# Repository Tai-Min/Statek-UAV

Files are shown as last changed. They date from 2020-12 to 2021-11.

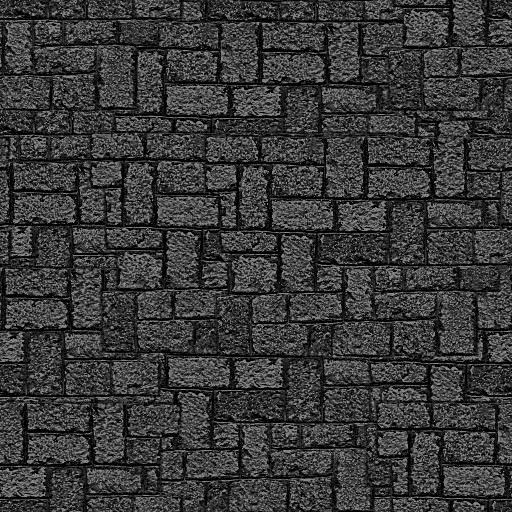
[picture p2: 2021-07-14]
catkin_ws/src/statek_sim/models/park_map/meshes/stone_dark.jpg

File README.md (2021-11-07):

# Statek-UAV
ROS based UAV, Master's degree final project.

This repository consists of CAD files for the chassis, CAD files for electronic boards, catkin workspace for all ROS nodes created for the project and some additional scripts used during development.

The core part of this project is the real, 3D printed vehicle along with all the hardware attached to it (Jetson Nano B01 for main controller and STM32f103RBT6 for real time core). 

The software part of this project can be split into real time (closed loop wheel control), short term navigation (movement between two GPS waypoints) and long term navigation (navigation through series of GPS waypoints).
During the project's development, my main focus was on short term navigation, which is also the biggest and most complicated part of the project. Short term navigation stack
consists of static local map generator, dynamic local map generator (human leg detector mostly based on U-Net fully convolutional neural network), Voronoi graph generator, A* path planner and non linear model predictive controller for navigation.

For more info see [this arcitle](https://www.hackster.io/Tai-Min/statek-uav-ff225e).

**Just to warn you:** If you want to use this project somehow, use it as reference only. It is NOT meant to be assembled as it contains some design flaws both in hardware
and software that I don't intent to fix in this iteration of the project as code in this repository will stay in unchanged since the moment I handed over my thesis.
Most of the files in the "instructions" folder consists of the steps I've did to setup my hardware and Ipopt solver. Those might not work for you/could be dangerous (I might've abused sudo a bit) so use them at your own risk. The code quality depends on the time I had untill the deadline to hand over my thesis. In my opinion it should be fine for the most part, well documented and easy to follow but judge for yourself.

**Disclaimer:** I've tried to credit all authors of 3D files used in the project. All of the models had permissive license allowing me to use them.
If you see your work here without being credited or you just don't want to have your files used here - open an issue on this project and I'll fix any problems.

The files in this folder have the following structure:
* CAD
  * detailed - Inventor files for the 3D printing and assembling.
  * low_poly - Inventor files for simple low poly model for Gazebo and Rviz.
* catkin_ws/src
  * statek - Metapackage for the project
  * statek_calibrate - Calibration algorithms for cameras, GPS Kalman filter, IMU, Motor's PI controller autotuning. 
  * statek_config - Config files for the robot, including transformations, urdf and parameters for ROS nodes.
  * statek_hw - code to launch hardware based nodes (lidar, rosserial, cameras etc.) along with source code for real time controller.
  * statek_map - Mapping algorithms (dynamic local mapper, voronoi generator and GPS to hyperplane casting).
  * statek_ml - Leg detector based mostly on U-net fully convolutional neural network
  * statek_nav - Navigation algorithms (NMPC and GPS waypoint follower script).
  * statek_plan - A* path planner for short term navigation.
  * statek_playground - Simple launch nodes to play with the hardware.
  * statek_rviz - Rviz visualization files.
  * statek_sim - Gazebo simulation files.
  * statek_srv - Server files to communicate with web application (really rough draft).
  * statek_teleop - Teleoperation nodes for Dualshock 4 gamepad.
* electronics
  * AM4096_encoder - KiCad's files for AM4096 encoder board.
  * Nucleo_screw_shield - KiCad's files for screw shield that fits morpho connector.
  * button_panel - Unused in the project.
  * connections - Electrical connections of the project.
* instructions - Rough draft of what I did to setup the robot.
* media - Contains camera's calibration chessboard.
* thesis_scripts - Some files used to add more value to the project.

Title

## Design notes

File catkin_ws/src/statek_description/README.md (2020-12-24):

# statek_description
Package with Statek's robot description files.
* **urdf**
  * **statek.urdf** Statek's robot description file used for Gazebo and Rviz.

    | args | description |
    |-|-|
    | statek_name | Name of current Statek UAV. Used to create namespace for Gazebo plugins and tf links. Default is statek. |

    | subscribed topics (when run in Gazebo) | |
    |-|-|
    | <statek_name>/vel_cmd_left | Velocity setpoint for left motor. |
    | <statek_name>/vel_cmd_right | Velocity setpoint for right motor. |

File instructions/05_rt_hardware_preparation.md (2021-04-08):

# Real time hardware

## Install necessary libraries
In PlatformIO terminal type:
```
pio lib -g install https://github.com/Tai-Min/MPU9250/archive/refs/heads/no-verbose.zip
```

## Compile and upload rt code
Connect STM board to PC.

Find source code:
```
roscd statek_hw/rt_src
```
Open it on Windows in VS code with PLATFORMIO plugin, and compile then upload the code.

Additionaly, you can change content of /include/config.hpp to change encoder addresses or tf links.

Previous: [Remote environment setup](https://github.com/Tai-Min/Statek-UAV/blob/master/instructions/04_remote_environment_setup.md)</br>
Next: [Sensor calibration](https://github.com/Tai-Min/Statek-UAV/blob/master/instructions/06_sensor_calibration.md)

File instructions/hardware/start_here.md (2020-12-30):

# Hardware preparation
## Assembly

## Cable connections

## Software preparation
When chassis is assembled and all the sensors are connected to Jetson / Nucleo, follow [Software preparation](https://github.com/Tai-Min/Statek-UAV/blob/master/instructions/software/start_here.md)

## Sensor calibration
Follow [Sensor calibration](https://github.com/Tai-Min/Statek-UAV/blob/master/instructions/hardware/sensor_calibration.md)

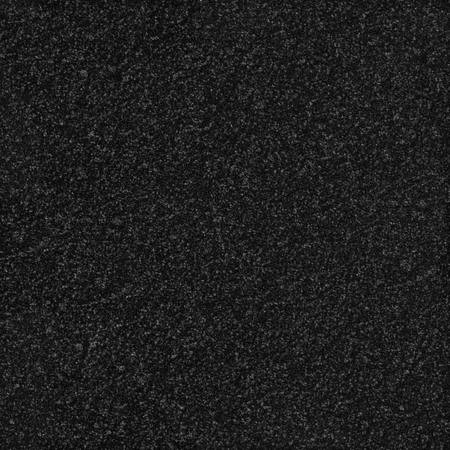
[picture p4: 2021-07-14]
catkin_ws/src/statek_sim/models/park_map/meshes/asphalt.jpg

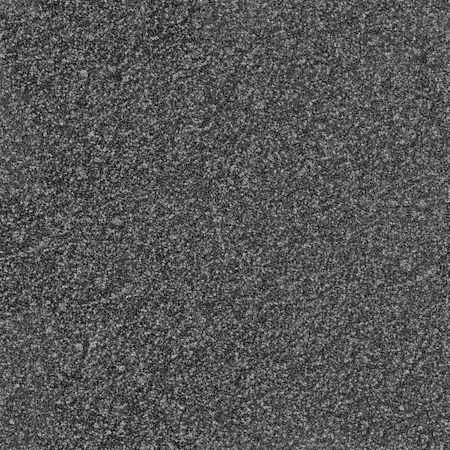
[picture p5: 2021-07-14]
catkin_ws/src/statek_sim/models/park_bench/meshes/stone.jpg

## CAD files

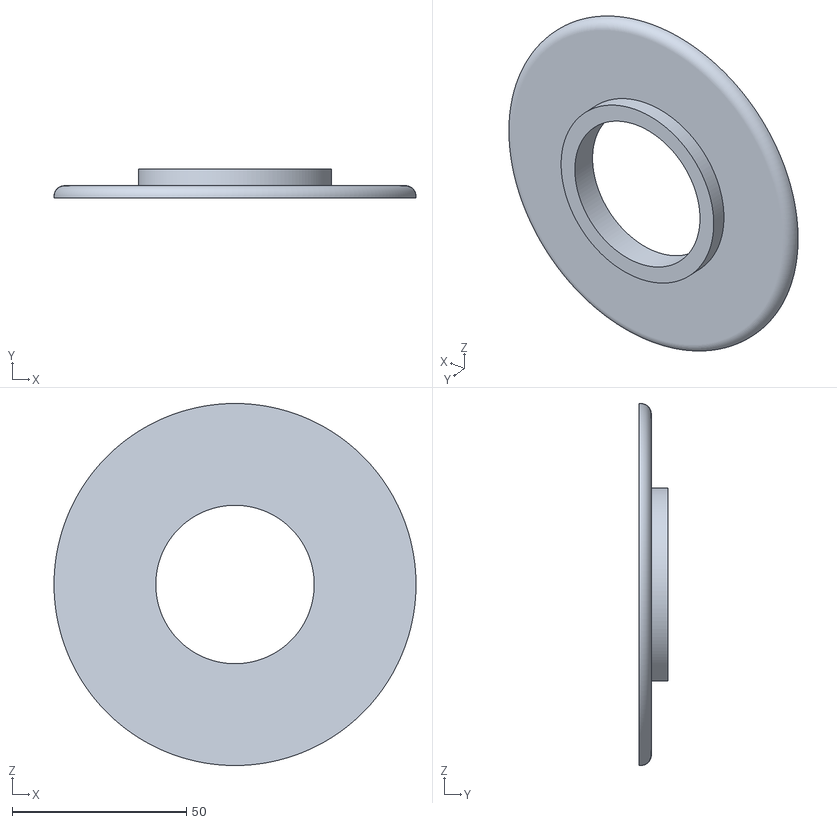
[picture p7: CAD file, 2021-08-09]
CAD/detailed/stl/motor_chain_guide_center.stl
104.0 x 8.25 x 104.0

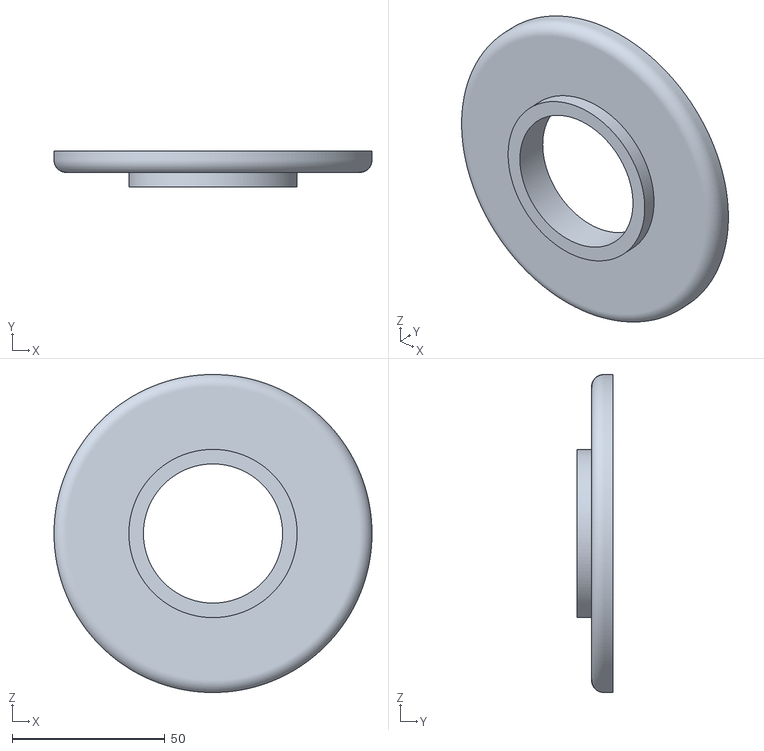
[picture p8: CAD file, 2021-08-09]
CAD/detailed/stl/wheel_chain_guide.stl
104.0 x 11.8 x 104.0

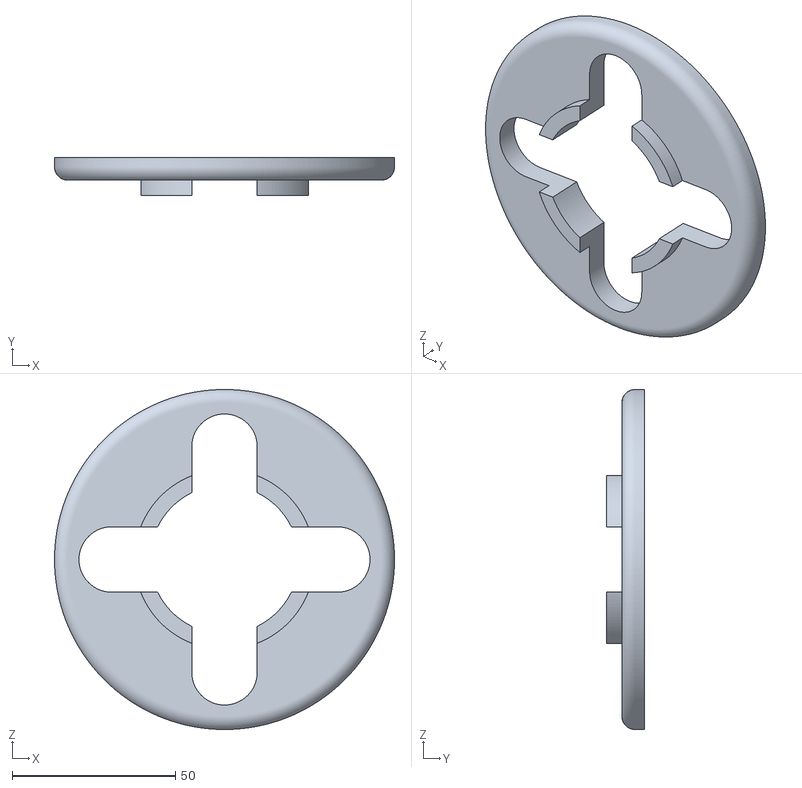
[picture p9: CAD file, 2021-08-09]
CAD/detailed/stl/wheel_chain_guide_holes.stl
104.0 x 11.8 x 104.0

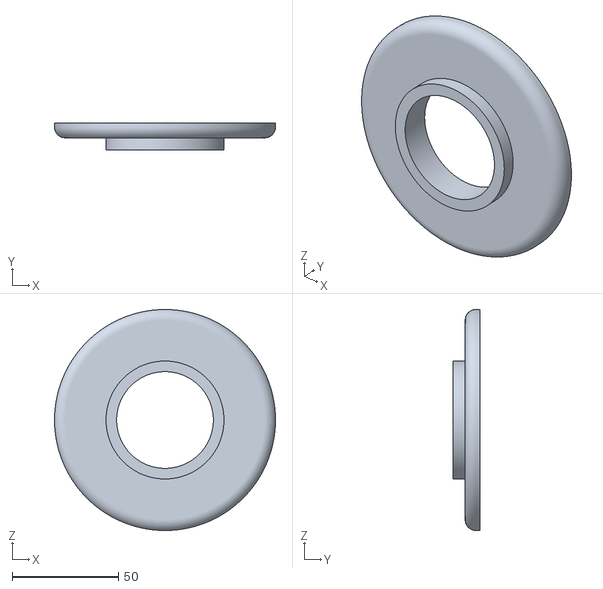
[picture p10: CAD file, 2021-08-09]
CAD/detailed/stl/motor_chain_guide_outer.stl
104.0 x 12.8 x 104.0

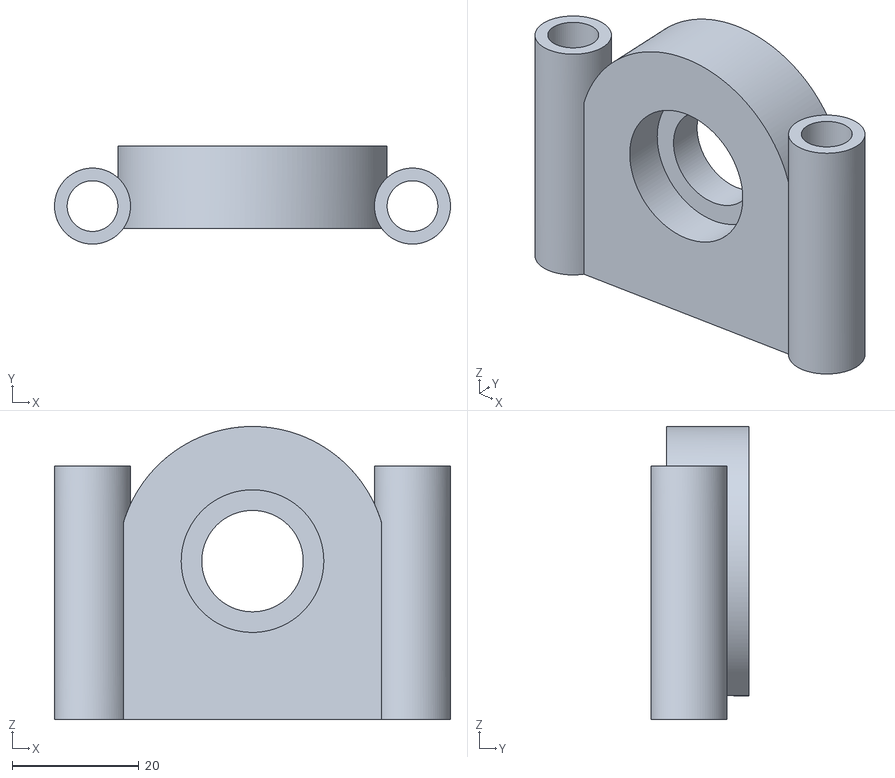
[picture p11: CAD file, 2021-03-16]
CAD/detailed/stl/wheel_stabilizer.stl
62.5 x 15.5 x 46.2

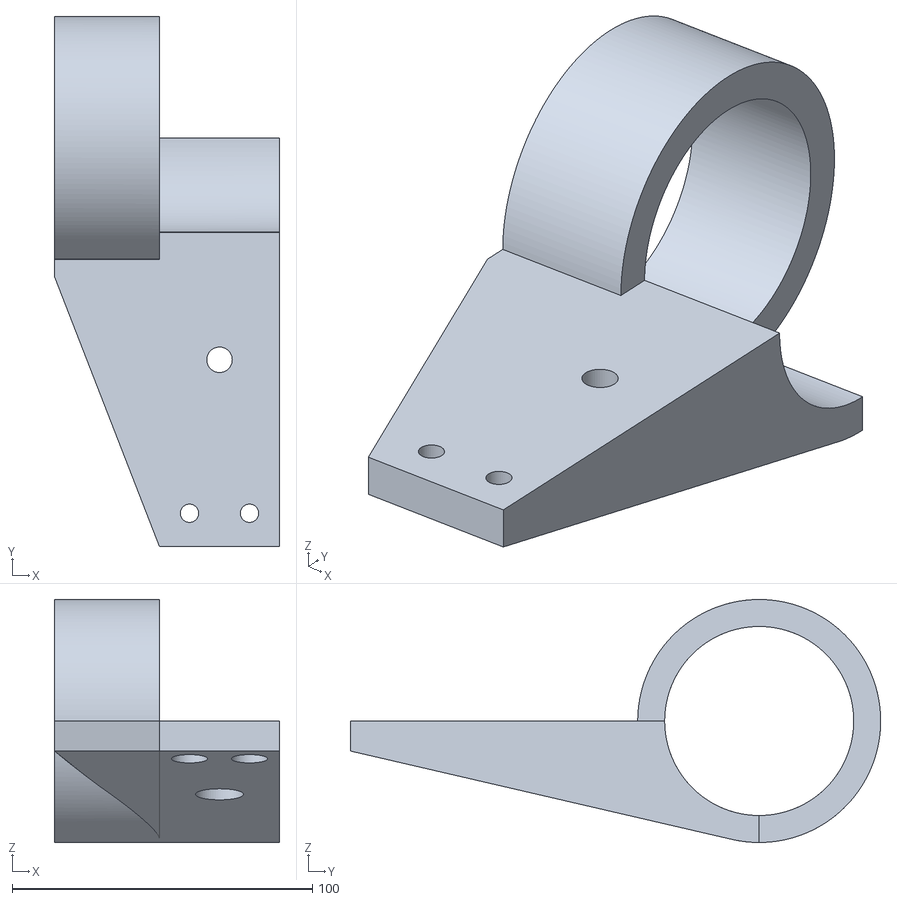
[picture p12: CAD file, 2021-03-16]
CAD/detailed/stl/motor_tensioner_left.stl
75.0 x 176.8 x 81.0

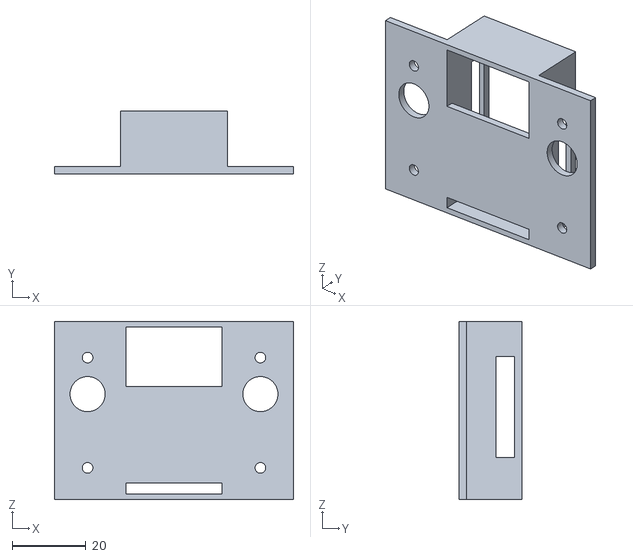
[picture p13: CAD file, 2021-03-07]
CAD/detailed/stl/voltometer_socket.stl
65.0 x 17.0 x 48.5

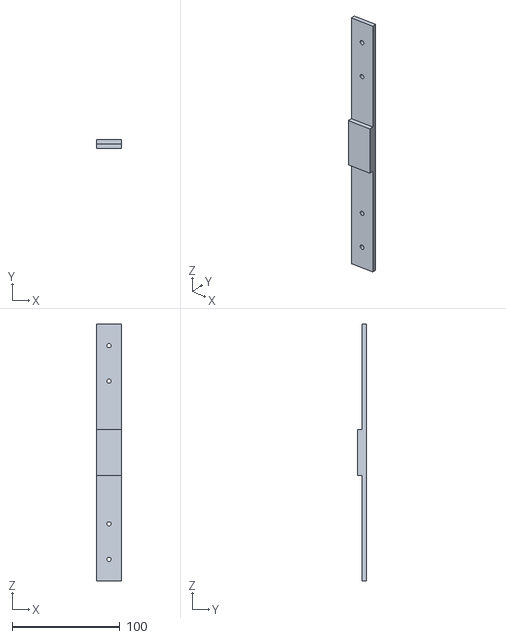
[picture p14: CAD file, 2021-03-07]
CAD/detailed/stl/battery_support.stl
23.0 x 8.15 x 238.8

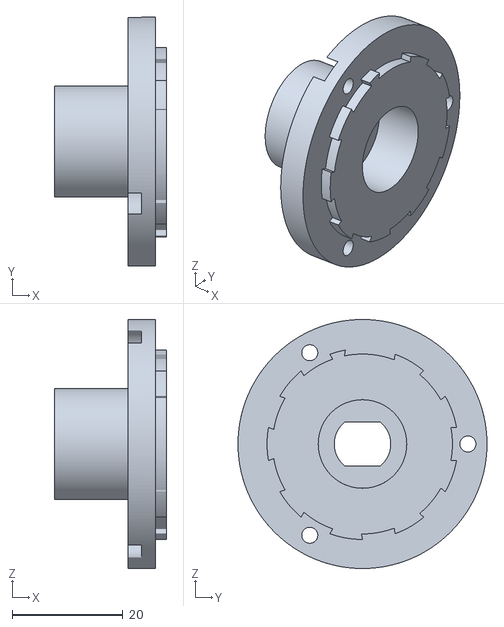
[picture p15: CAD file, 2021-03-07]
CAD/detailed/stl/motor_gearing_short.stl
20.2 x 45.0 x 45.0

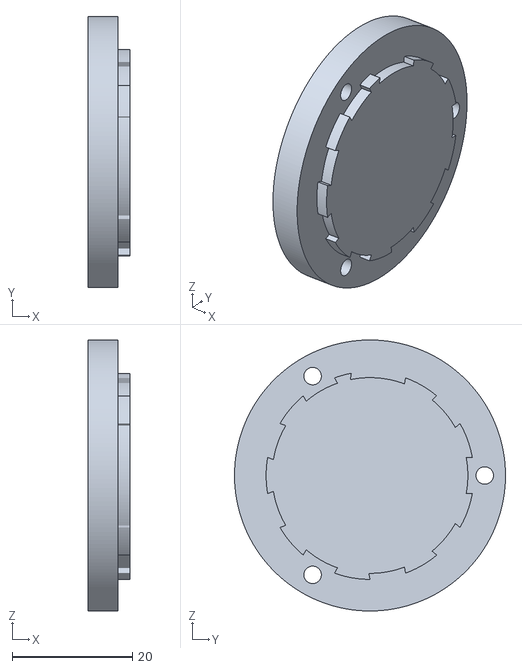
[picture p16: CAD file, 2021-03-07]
CAD/detailed/stl/motor_gearing_cover.stl
7.00 x 45.0 x 45.0

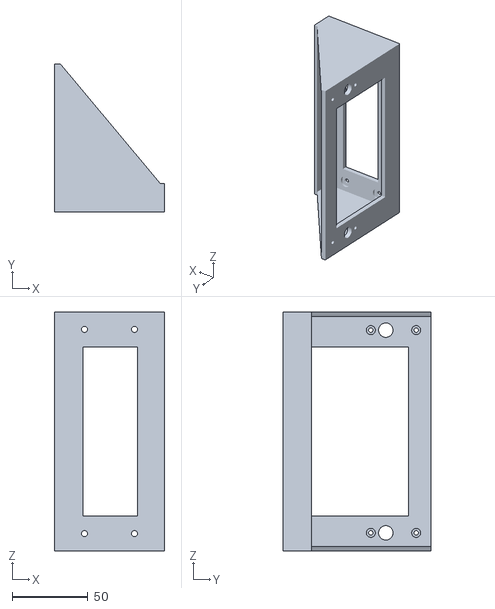
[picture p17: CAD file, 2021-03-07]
CAD/detailed/stl/battery_box.stl
73.0 x 98.0 x 158.0

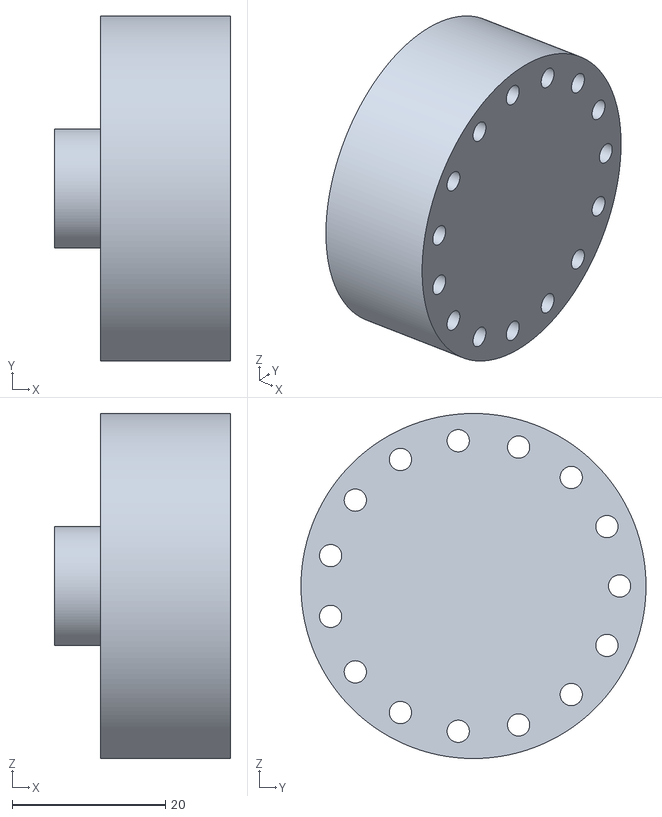
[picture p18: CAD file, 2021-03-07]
CAD/detailed/stl/motor_gearing_long.stl
23.0 x 45.0 x 45.0

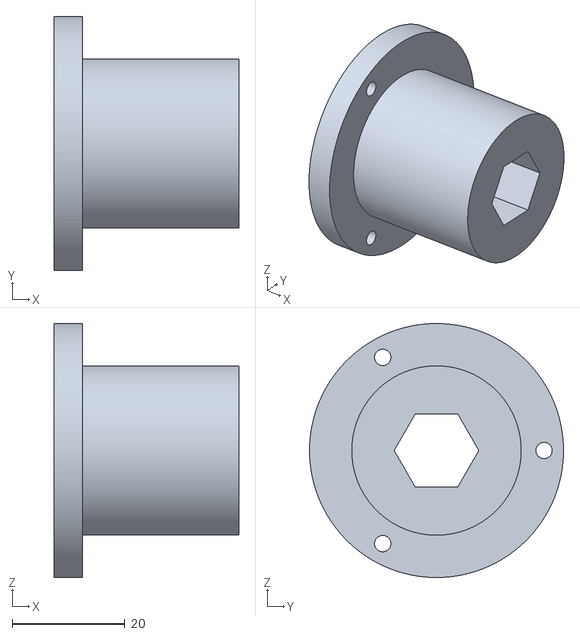
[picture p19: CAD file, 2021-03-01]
CAD/detailed/stl/wheel_gearing_mount_long.stl
32.8 x 45.0 x 45.0

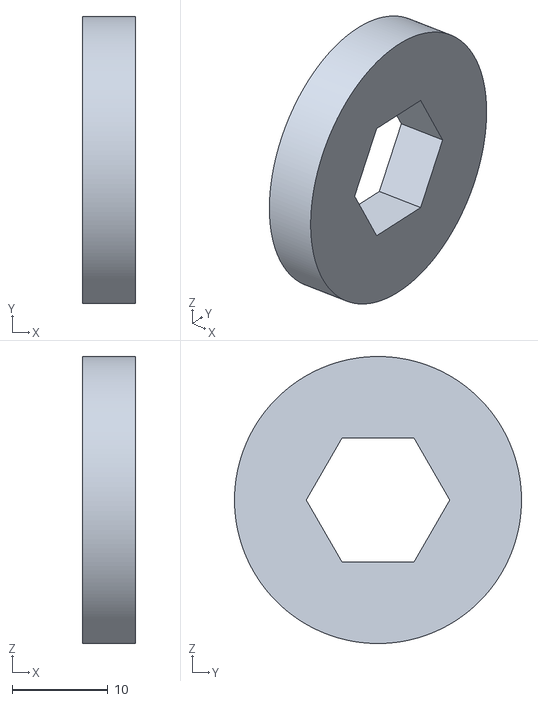
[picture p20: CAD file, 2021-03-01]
CAD/detailed/stl/wheel_gearing_mount_extension.stl
5.50 x 30.0 x 30.0

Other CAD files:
CAD/detailed/stl/motor_tensioner_right.stl
CAD/detailed/stl/wheel_gearing_mount_short.stl
CAD/detailed/stl/encoder_cover.stl
CAD/detailed/stl/wheel_connector.stl
CAD/detailed/base.ipt
CAD/detailed/battery.ipt
CAD/detailed/battery_box.ipt
CAD/detailed/battery_support.ipt
CAD/detailed/converter_case.ipt
CAD/detailed/damping_system_housing_connector.ipt
CAD/detailed/din_connector.ipt
CAD/detailed/din_connector_back.ipt
CAD/detailed/din_connector_center.iam
CAD/detailed/din_connector_front.ipt
CAD/detailed/din_connector_wheel.iam
CAD/detailed/din_motor_connector.ipt
CAD/detailed/din_wheel_connector.ipt
CAD/detailed/encoder_cover.ipt
CAD/detailed/encoder_magnet_socket.ipt
CAD/detailed/gps_antenna_cover.ipt
CAD/detailed/gps_cable_holder.ipt
CAD/detailed/gps_plate.ipt
CAD/detailed/imu_cable_holder.ipt
CAD/detailed/imu_plate.ipt
CAD/detailed/jetson_case.ipt
CAD/detailed/lidar_plate.ipt
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

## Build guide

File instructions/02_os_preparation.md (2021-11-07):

# OS preparation
## Jetson Nano OS preparation
Install Jetson Nano OS as described [here](https://developer.nvidia.com/embedded/learn/get-started-jetson-nano-devkit). </br></br>
Reinstall libcanberra-gtk-module:
```
sudo apt-get install --reinstall libcanberra-gtk-module
```

Install required python modules:
```
sudo apt-get install python-numpy python-scipy python-matplotlib ipython python-pandas python-sympy python-nose
sudo apt-get install gfortran
pip2 install scipy
pip2 install astar
```
## Configure wifi
Find name of your wifi device:
```
ifconfig
```
Enable it:
```
ifconfig <your wifi card/dongle>
```
Add it to interfaces:
```
sudo nano /etc/network/interfaces
```
And insert this:
```
auto <your wifi card/dongle>
iface <your wifi card/dongle> inet dhcp
  wpa-ssid <ssid>
  wpa-psk <password>
```
Save file.

Connect to wifi:
```
sudo dhclient <your wifi card/dongle>
```
Now, you should be able to connect to the UAV and control it without wired connection.

## Configure serial devices
Make sure that all serial devices are connected.

### Disable UART console
```
systemctl stop nvgetty
systemctl disable nvgetty
udevadm trigger
```

### Add yourself to dialout group
```
sudo usermod -a -G dialout $USER
```

### Add your lidar info to udev rules
Find info about your device (idVendor, idProduct, serial):
```
udevadm info -a -p  $(udevadm info -q path -n /dev/ttyUSBn)
```

Where /dev/ttyUSBn is the port to which your lidar is connected to.

Add new rule to udev:
```
sudo nano /etc/udev/rules.d/99-usb-serial.rules
```

Then add this line:
```
SUBSYSTEM=="tty", ATTRS{idVendor}=="<YOUR ID>", ATTRS{idProduct}=="<YOUR ID>", ATTRS{serial}=="<YOUR SERIAL>", SYMLINK+="ydlidar"
```

### Add STM board to udev rules
Repeat steps from "Add your lidar info to udev rules", find device with:
```
ATTRS{manufacturer}=="STMicroelectronics"
```
And add it to udev under lidar as:
```
SUBSYSTEM=="tty", ATTRS{idVendor}=="<YOUR ID>", ATTRS{idProduct}=="<YOUR ID>", ATTRS{serial}=="<YOUR SERIAL>", SYMLINK+="stm"
```

## Finishing up
### Reboot machine 
```
sudo reboot
```
Previous: [Electronics connections](https://github.com/Tai-Min/Statek-UAV/blob/master/instructions/01_electronics_connections.md) </br>
Next: [ROS](https://github.com/Tai-Min/Statek-UAV/blob/master/instructions/03_ros.md)

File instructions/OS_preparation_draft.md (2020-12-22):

[Previous step - Third party packages](https://github.com/Tai-Min/Statek-UAV/blob/master/instructions/thirdparty_packages.md)

# OS preparation

## Serial device preparation
### Add yourself to dialout group
```
sudo usermod -a -G dialout $USER
```

### Add your lidar info to udev rules
Find info about your device (idVendor, idProduct, serial):
```
udevadm info -a -p  $(udevadm info -q path -n /dev/ttyUSBn)
```

Where /dev/ttyUSBn is the port to which your lidar is connected to.

Add new rule to udev (as sudo):
```
sudo nano /etc/udev/rules.d/99-usb-serial.rules
```

Then add this line:
```
SUBSYSTEM=="tty", ATTRS{idVendor}=="<YOUR ID>", ATTRS{idProduct}=="<YOUR ID>", ATTRS{serial}=="<YOUR SERIAL>", SYMLINK+="ydlidar"
```

### Reboot machine 
```
sudo reboot
```

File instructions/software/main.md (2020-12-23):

# Software preparation

## Jetson Nano OS preparation
Install Jetson Nano OS as described [here](https://developer.nvidia.com/embedded/learn/get-started-jetson-nano-devkit).

After that, follow [OS preparation](https://github.com/Tai-Min/Statek-UAV/blob/master/instructions/software/OS_preparation.md) part and when completed, return here to setup ROS environment.

## Setting up ROS 
Install ROS Melodic Morenia as described [here](http://wiki.ros.org/melodic/Installation/Ubuntu).

After that, setup your catkin workspace as described in [here](http://wiki.ros.org/catkin/Tutorials/create_a_workspace).

## Setting up ROS packages
Copy content of this repository's catkin_ws/src content into your catkin_ws/src folder and run :
```
catkin_make 
```
inside you catkin workspace.

Now, install third party packages:
* [ds4_driver](http://wiki.ros.org/ds4_driver)
* [ydlidar_ros](https://github.com/YDLIDAR/ydlidar_ros)

Now, in your catkin_ws folder run:
```
find . -type f -name "*.py" -print0 | xargs -0 chmod +x
```
To make all python nodes executable.

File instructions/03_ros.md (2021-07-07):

# ROS
## Install Eigen
In user directory:
```
git clone https://gitlab.com/libeigen/eigen.git
cd eigen
mkdir build
cd build
cmake ..
make
sudo make install 
```
## Install Ipopt and  MUMPS
Install Ipopt and MUMPS as described [here](https://coin-or.github.io/Ipopt/INSTALL.html) (Perform MUMPS steps in home directory).
For Ipopt's configure step type:
```
ldconfig
export CPLUS_INCLUDE_PATH=/usr/include/mpi:$CPLUS_INCLUDE_PATH
export LIBRARY_PATH=/usr/lib/openmpi/lib:$LIBRARY_PATH
../configure --with-mumps-cflags="-I$HOME/ThirdParty-Mumps/MUMPS/include -DCMAKE_CXX_COMPILER=/usr/bin/mpic++" --with-mumps-lflags="-pthread -L/usr//lib -L/usr/lib/aarch64-linux-gnu/openmpi/lib -lmpi_cxx -lcoinmumps" --without-hsl
```
Also install [CppAD](https://www.coin-or.org/CppAD/Doc/install.htm).

## Setting up ROS 
Install ROS Melodic Morenia as described [here](http://wiki.ros.org/melodic/Installation/Ubuntu).

After that, setup your catkin workspace as described in [here](http://wiki.ros.org/catkin/Tutorials/create_a_workspace).

## Setting up ROS packages
Copy content of this repository's catkin_ws/src content into your catkin_ws/src folder.

Now, install third party packages:
* [ds4_driver](http://wiki.ros.org/ds4_driver)
* [ydlidar_ros](https://github.com/YDLIDAR/ydlidar_ros)
* [nmea_navsat_driver](http://wiki.ros.org/nmea_navsat_driver)
* [rosserial](https://github.com/ros-drivers/rosserial) (select melodic branch to clone)
* [hector_gazebo_plugins](https://wiki.ros.org/hector_gazebo_plugins)

cd into rosserial:
```
roscd rosserial_python/src/rosserial_python
```
open SerialClient.py and repleace:
```
import queue
```
with:
```
import Queue as queue
```

Now, in your catkin_ws folder run:
```
find . -type f -name "*.py" -print0 | xargs -0 chmod +x
```
To make all python nodes executable.

Edit cv_bridge's config:
```
sudo nano /opt/ros/melodic/share/cv_bridge/cmake/cv_bridgeConfig.cmake
```
Search for lines:
```
if(NOT "include;/usr/include;/urs/include/opencv " STREQUAL " ")
...
set(_include_dirs "include;/usr/include;/urs/include/opencv")
```
And replace them with:
```
if(NOT "include;/usr/include;/usr/include/opencv4 " STREQUAL " ")
...
set(_include_dirs "include;/usr/include;/usr/include/opencv4")
```
Save file.

Lastly, run:
```
catkin_make 
```
inside you catkin workspace.

Previous: [OS preparation](https://github.com/Tai-Min/Statek-UAV/blob/master/instructions/02_os_preparation.md) </br>
Next: [Remote environment setup](https://github.com/Tai-Min/Statek-UAV/blob/master/instructions/04_remote_environment_setup.md)

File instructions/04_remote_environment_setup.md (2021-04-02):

# Remote environment setup

## Setup WSL 2
### Setup Ubuntu subsystem for windows
https://docs.microsoft.com/en-us/windows/wsl/install-win10

### Then setup GUI for WSL 2
https://medium.com/@japheth.yates/the-complete-wsl2-gui-setup-2582828f4577

**Note:** Always start VcXsrv with -nowgl parameter and access control disabled.

### Setup ROS
Just repeat [03_ros.md](https://github.com/Tai-Min/Statek-UAV/blob/master/instructions/03_ros.md) again.

### Establish connection with UAV
To be able to use Rviz or Gazebo on WSL that will communicate with rosmaster node on the UAV, type:
```
export ROS_MASTER_URI=http://<ip of the vehicle>:11311
```
in your WSL terminal every time you start it. </br>

You can add this line to your .bashrc file for convenience.

### ~/.bashrc
Make sure you have all of these lines added to the end of your ~/.bashrc file:
```
export DISPLAY=$(cat /etc/resolv.conf | grep nameserver | awk '{print $2; exit;}'):0.0
export LIBGL_ALWAYS_INDIRECT=
/etc/init.d/dbus start &> /dev/null
source /opt/ros/melodic/setup.bash
source <path to catkin_ws folder>/devel/setup.bash
export ROS_MASTER_URI=http://<ip of the vehicle>:11311
export GCC4MBED_DIR=~/gcc4mbed
export ROS_LIB_DIR=~/ros/lib/ros_lib
```

## VS Code setup
Instal Remote - SSH and PlatformIO extensions.

Previous: [ROS](https://github.com/Tai-Min/Statek-UAV/blob/master/instructions/03_ros.md)</br>
Next: [Real time hardware](https://github.com/Tai-Min/Statek-UAV/blob/master/instructions/05_rt_hardware_preparation.md)

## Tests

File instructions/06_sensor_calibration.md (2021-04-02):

# Sensor calibration
## Prepare UAV
Run:
```
roslaunch statek_hw statek.launch
```
And restart it after every calibration step to load calibrated params.

## Motion calibration
On Jetson nano run:
```
roslaunch statek_calibrate motion_calibrator.launch
```
And follow instructions.

## Battery calibration
On Jetson nano edit your statek_calibrate/yaml/battery_config.yaml to match your battery.

## Camera calibration
Before anything, check statek_config/yaml/camera_config.yaml and set parameters to match your camera (default are for original raspi cam 2) (Dont' touch width and height parameters!).

Print </br> 
Chessboard </br> 
and measure width of one black square.

On WSL 2 run once:
```
rosdep install camera_calibration
rosmake camera_calibration
```
Then every time you want to calibrate the camera run:
```
roslaunch statek_calibrate camera_info_calibrator.launch square_size:=<SIZE OF BLACK SQUARE IN METERS>
```
Follow [camera_calibration](http://wiki.ros.org/camera_calibration/Tutorials/StereoCalibration) from point 4.
If the result is satisfying then click COMMIT button and kill launch file and proceed to next step. If camera_calibration node returned some errors / can't communicate with vision node then you can copy content of **D, K, P, R** matrices into **statek_config/yaml/camera_info_left.yaml** and **statek_config/yaml_camera_info_right.yaml**

## Depth calibration
On WSL 2 run:
```
roslaunch statek_calibrate depth_calibrator.launch
```
In rqt reconfigure window navigate to statek/stereo/stereo_image_proc and tune parameters so disparity window and point cloud in Rviz looks good. Save parameters using rqt reconfigure gui into statek_calibrate package into /yaml/ folder as depth_config.yaml

Move this file to UAV using:
```
scp <PATH TO LOCAL CATKIN WS>/statek_calibrate/yaml/depth_config.yaml <UAV's username>@<UAV's ip>:<PATH TO UAV CATKIN WS>/statek_calibrate/yaml/depth_config.yaml
```

## Troubleshooting
If something in real UAV does not match Rviz's visualization, try to play with static transforms located in statek_config/tf as all the transforms can vary, depending on your print quality and assembly.</br>
  
* Lidar tf calibration </br>
Run statek_hw/statek.launch and statek_rviz/view.launch.
Open tf/base_to_laser file from statek_config package in text editor and edit fourth parameter so PointCloud2 and LaserScan match in Rviz window.

Previous: [Real time hardware](https://github.com/Tai-Min/Statek-UAV/blob/master/instructions/05_rt_hardware_preparation.md) </br>
Next: []()

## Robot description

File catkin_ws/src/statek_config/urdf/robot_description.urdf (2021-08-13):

<?xml version="1.0" ?>
<robot name="statek" xmlns:xacro="http://www.ros.org/wiki/xacro">
  <xacro:arg name="statek_name" default="statek"/>

  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

  <xacro:arg name="lat" default="54.386279"/>
  <xacro:arg name="lon" default="18.590767"/>

  <xacro:arg name="mu1" default="0.00"/>
  <xacro:arg name="mu2" default="0.00"/>
  <xacro:arg name="kp" default="100000"/>
  <xacro:arg name="kd" default="1"/>
  <xacro:arg name="fdir1" default="0 0 1"/>

  <xacro:property name="motion_config" value="${load_yaml('$(find statek_config)/yaml/motion_config.yaml')}"/>
  <xacro:property name="max_velocity_rads" value="${motion_config['wheel_max_angular_velocity']}"/>
  <xacro:property name="distance_between_wheels" value="${motion_config['distance_between_wheels']}"/>
  <xacro:property name="wheel_radius" value="${motion_config['wheel_radius']}"/>

  <xacro:property name="camera_config" value="${load_yaml('$(find statek_config)/yaml/camera_config.yaml')}"/>
  <xacro:property name="camera_width" value="${camera_config['width']}"/>
  <xacro:property name="camera_height" value="${camera_config['height']}"/>
  <xacro:property name="camera_framerate" value="${camera_config['framerate']}"/>
  <xacro:property name="camera_hfov" value="${camera_config['horizontal_fov']}"/>
  <xacro:property name="camera_vfov" value="${camera_config['vertical_fov']}"/>

  <xacro:property name="camera_info_left" value="${load_yaml('$(find statek_config)/yaml/camera_info_left.yaml')}"/>
  <xacro:property name="camera_info_D" value="${camera_info_left['D']}"/>
  <xacro:property name="camera_info_K" value="${camera_info_left['K']}"/>

  <joint name="left_back_wheel_hinge" type="revolute">
    <parent link="$(arg statek_name)/base_link"/>
    <child link="$(arg statek_name)/wheels/left_back_link"/>
    <origin rpy="0 0 1.5708" xyz="-0.252682 0.270467 -0.03126"/>
    <axis xyz="1 0 0"/>
    <limit effort="-1" lower="-1e16" upper="1e16" velocity="-1"/>
  </joint>

  <joint name="right_back_wheel_hinge" type="revolute">
    <parent link="$(arg statek_name)/base_link"/>
    <child link="$(arg statek_name)/wheels/right_back_link"/>
    <origin rpy="0 0 1.5708" xyz="-0.252682 -0.264541 -0.03126"/>
    <axis xyz="1 0 0"/>
    <limit effort="-1" lower="-1e16" upper="1e16" velocity="-1"/>
  </joint>

  <joint name="left_front_wheel_hinge" type="revolute">
    <parent link="$(arg statek_name)/base_link"/>
    <child link="$(arg statek_name)/wheels/left_front_link"/>
    <origin rpy="0 0 1.5708" xyz="0.167807 0.270467 -0.03126"/>
    <axis xyz="1 0 0"/>
    <limit effort="-1" lower="-1e16" upper="1e16" velocity="-1"/>
  </joint>

  <joint name="right_front_wheel_hinge" type="revolute">
    <parent link="$(arg statek_name)/base_link"/>
    <child link="$(arg statek_name)/wheels/right_front_link"/>
    <origin rpy="0 0 1.5708" xyz="0.167807 -0.264541 -0.03126"/>
    <axis xyz="1 0 0"/>
    <limit effort="-1" lower="-1e16" upper="1e16" velocity="-1"/>
  </joint>

  <link name="$(arg statek_name)/base_link">

    <inertial>
      <mass value="9"/>
      <origin rpy="0 0 1.57" xyz="-0.04 0 0.012"/>
      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
    </inertial>

    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

  </link>

  <link name="$(arg statek_name)/wheels/left_back_link">

    <inertial>
      <mass value="1.3"/>
      <origin rpy="0 0 1.57" xyz="0.012 0 0"/>
      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
    </inertial>

    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

  </link>

  <link name="$(arg statek_name)/wheels/right_back_link">

    <inertial>
      <mass value="1.3"/>
      <origin rpy="0 0 1.57" xyz="0.012 0 0"/>
      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
    </inertial>

    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

  </link>

  <link name="$(arg statek_name)/wheels/left_front_link">

    <inertial>
      <mass value="1.3"/>
      <origin rpy="0 0 1.57" xyz="0.012 0 0"/>
      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
    </inertial>

    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

  </link>

  <link name="$(arg statek_name)/wheels/right_front_link">

    <inertial>
      <mass value="1.3"/>
      <origin rpy="0 0 1.57" xyz="0.012 0 0"/>
      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
    </inertial>

    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

  </link>

  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

</robot>

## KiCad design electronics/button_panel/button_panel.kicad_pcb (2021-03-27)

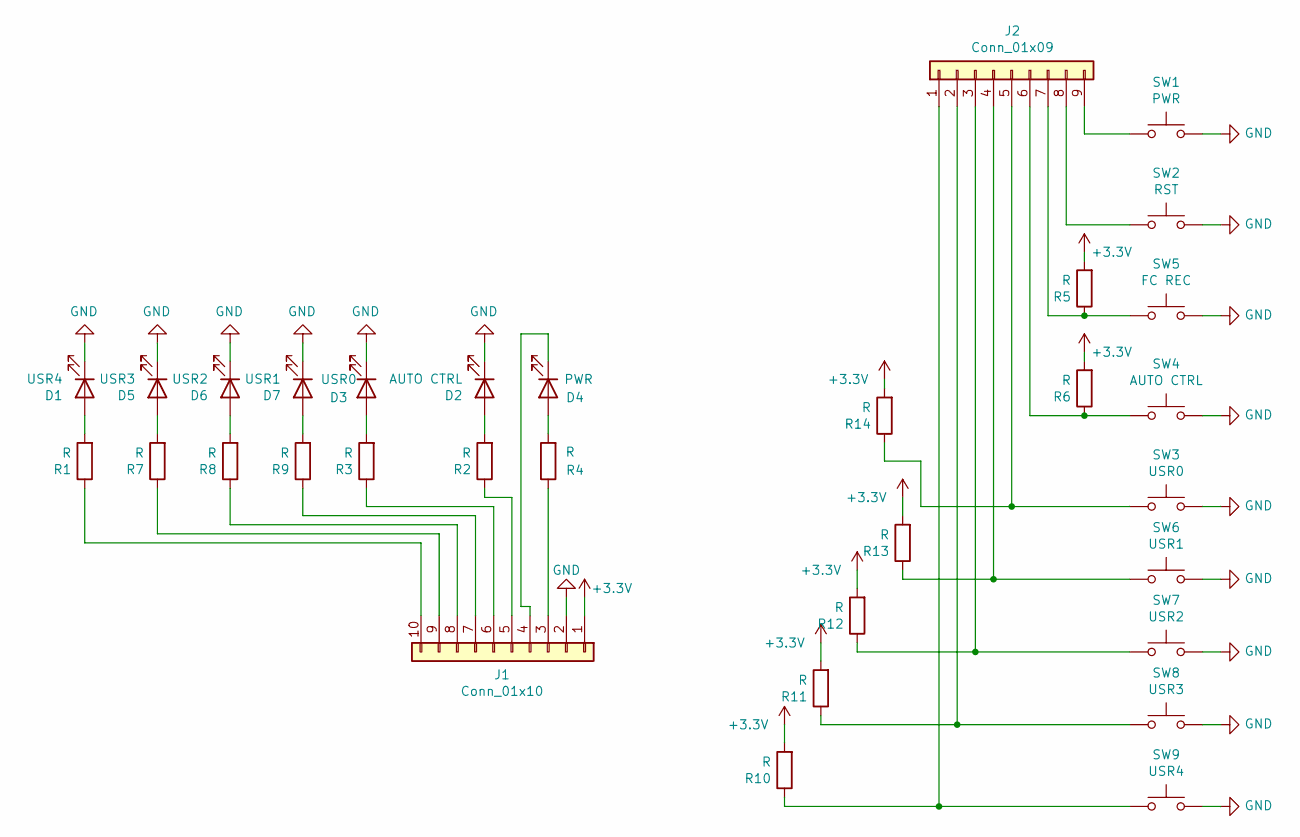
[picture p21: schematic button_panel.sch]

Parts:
D1: USR4; LED_D5.0mm_Clear
D2: AUTO CTRL; LED_D5.0mm_Clear
D3: USR0; LED_D5.0mm_Clear
D4: PWR; LED_D5.0mm_Clear
D5: USR3; LED_D5.0mm_Clear
D6: USR2; LED_D5.0mm_Clear
D7: USR1; LED_D5.0mm_Clear
J1: Conn_01x10; PinHeader_1x10_P2.54mm_Vertical
J2: Conn_01x09; PinHeader_1x09_P2.54mm_Vertical
R1, R2, R3, R4, R5, R6, R7, R8, R9, R10, R11, R12, R13, R14: R; R_1206_3216Metric_Pad1.42x1.75mm_HandSolder
SW1: PWR; SW_PUSH_6mm
SW2: RST; SW_PUSH_6mm
SW3: USR0; SW_PUSH_6mm
SW4: AUTO CTRL; SW_PUSH_6mm
SW5: FC REC; SW_PUSH_6mm
SW6: USR1; SW_PUSH_6mm
SW7: USR2; SW_PUSH_6mm
SW8: USR3; SW_PUSH_6mm
SW9: USR4; SW_PUSH_6mm

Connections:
+3V3: J1.1, R5.2, R6.2, R10.2, R11.2, R12.2, R13.2, R14.2
GND: D1.1 (K), D2.1 (K), D3.1 (K), D5.1 (K), D6.1 (K), D7.1 (K), J1.2, SW1.2, SW2.2, SW3.2, SW4.2, SW5.2, SW6.2, SW7.2, SW8.2, SW9.2
unnamed: D1.2 (A), R1.2
unnamed: D2.2 (A), R2.2
unnamed: D3.2 (A), R3.2
unnamed: D4.1 (K), J1.4
unnamed: D4.2 (A), R4.2
unnamed: D5.2 (A), R7.2
unnamed: D6.2 (A), R8.2
unnamed: D7.2 (A), R9.2
unnamed: J1.3, R4.1
unnamed: J1.5, R2.1
unnamed: J1.6, R3.1
unnamed: J1.7, R9.1
unnamed: J1.8, R8.1
unnamed: J1.9, R7.1
unnamed: J1.10, R1.1
unnamed: J2.1, R10.1, SW9.1
unnamed: J2.2, R11.1, SW8.1
unnamed: J2.3, R12.1, SW7.1
unnamed: J2.4, R13.1, SW6.1
unnamed: J2.5, R14.1, SW3.1
unnamed: J2.6, R6.1, SW4.1
unnamed: J2.7, R5.1, SW5.1
unnamed: J2.8, SW2.1
unnamed: J2.9, SW1.1

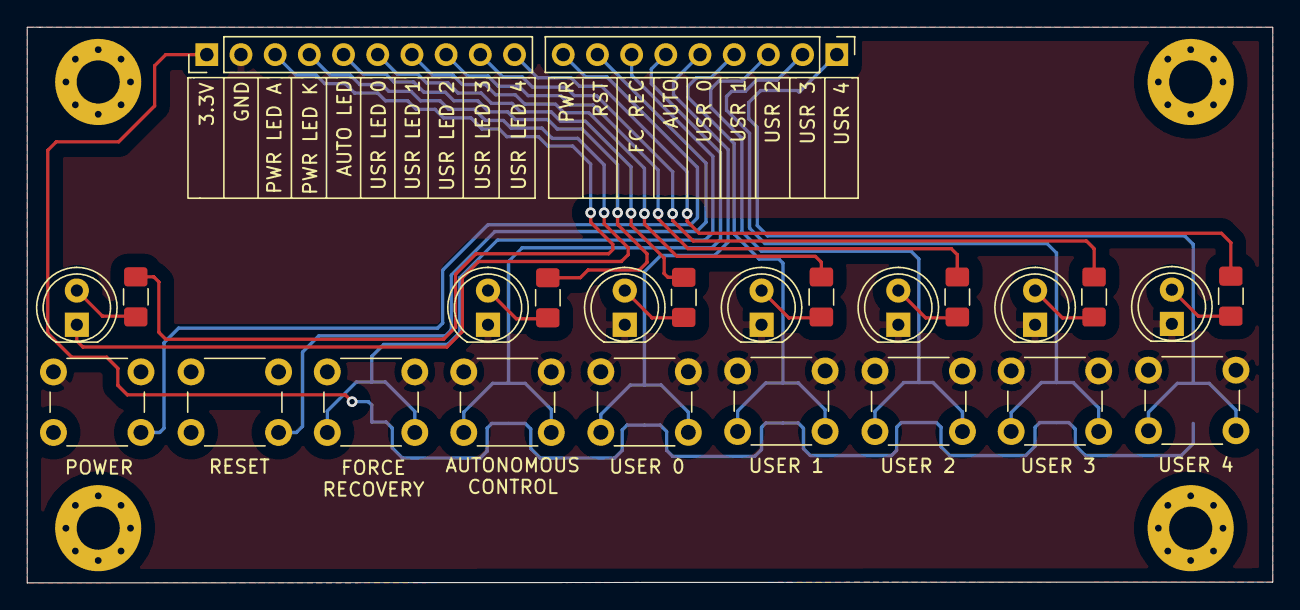
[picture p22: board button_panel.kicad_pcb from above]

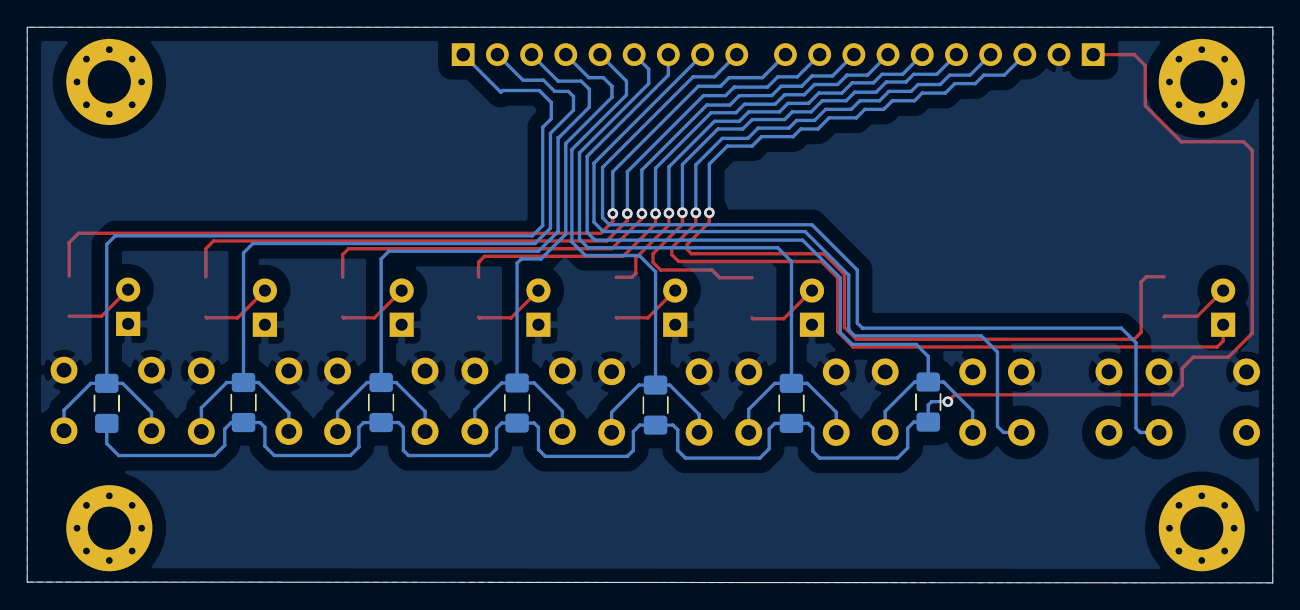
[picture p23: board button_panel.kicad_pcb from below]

Board: 2 copper layers, 92.5 x 41.3 mm, 32 parts (7 on the bottom side), 26 nets.

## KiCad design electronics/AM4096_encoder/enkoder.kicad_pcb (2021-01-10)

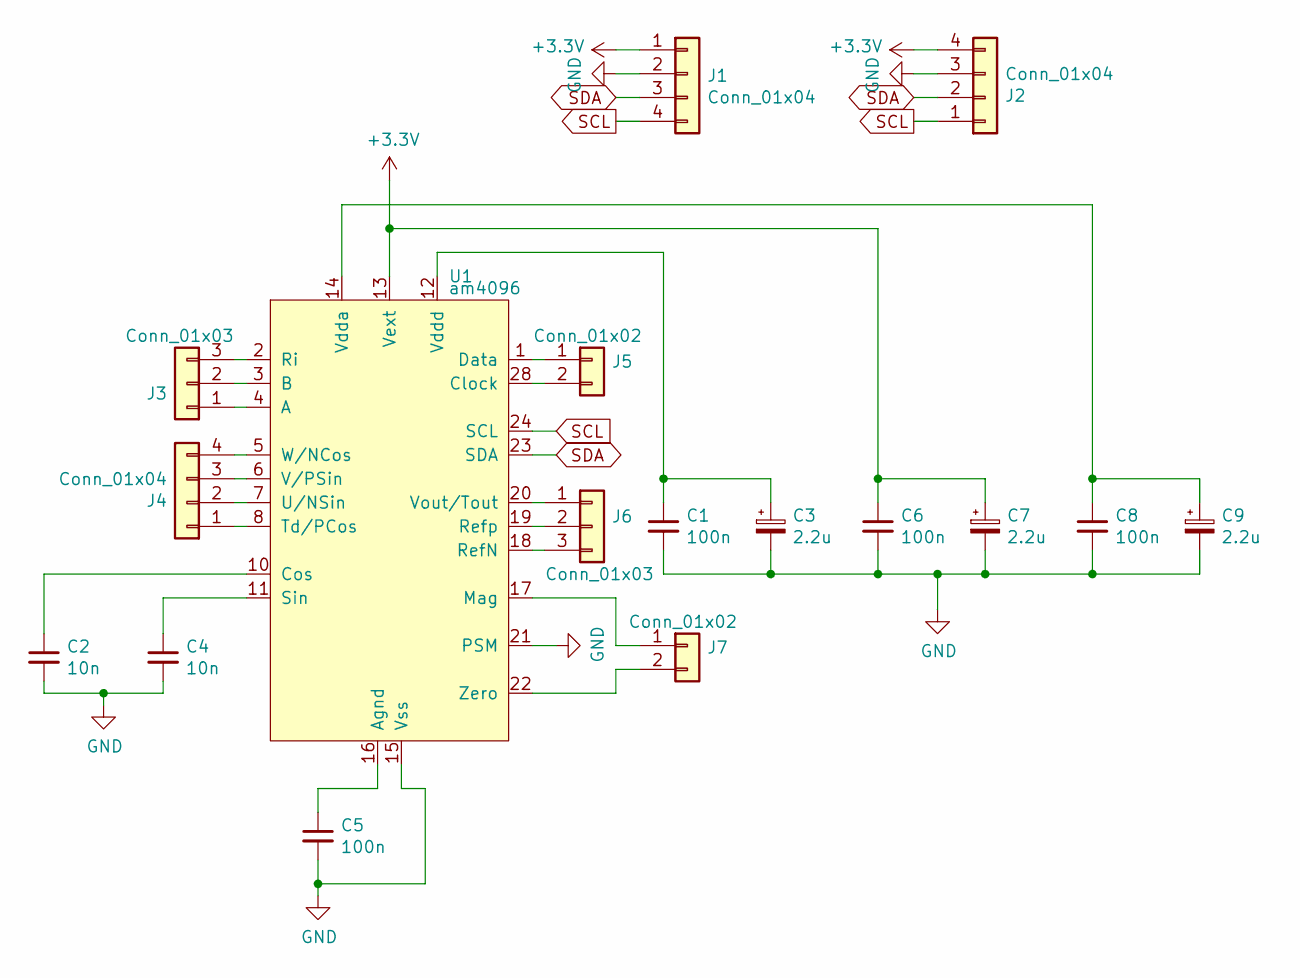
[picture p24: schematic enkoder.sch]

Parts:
C1, C5, C6, C8: 100n; C_1206_3216Metric_Pad1.42x1.75mm_HandSolder
C2, C4: 10n; C_1206_3216Metric_Pad1.42x1.75mm_HandSolder
C3, C7, C9: 2.2u; CP_EIA-3216-18_Kemet-A_Pad1.58x1.35mm_HandSolder
J1, J4: Conn_01x04; PinSocket_1x04_P2.54mm_Vertical
J2: Conn_01x04; TerminalBlock_MetzConnect_Type086_RT03404HBLC_1x04_P3.81mm_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
J3, J6: Conn_01x03; PinSocket_1x03_P2.54mm_Vertical
J5, J7: Conn_01x02; PinSocket_1x02_P2.54mm_Vertical
U1: am4096; SSOP-28_5.3x10.2mm_P0.65mm

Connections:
+3V3: C6.1, C7.1, J1.1, J2.4, U1.13 (Vext)
GND: C1.2, C2.2, C3.2, C4.2, C5.2, C6.2, C7.2, C8.2, C9.2, J1.2, J2.3, U1.15 (Vss), U1.21 (PSM)
unnamed: C1.1, C3.1, U1.12 (Vddd)
unnamed: C2.1, U1.10 (Cos)
unnamed: C4.1, U1.11 (Sin)
unnamed: C5.1, U1.16 (Agnd)
unnamed: C8.1, C9.1, U1.14 (Vdda)
unnamed: J3.1, U1.4 (A)
unnamed: J3.2, U1.3 (B)
unnamed: J3.3, U1.2 (Ri)
unnamed: J4.1, U1.8 (Td/PCos)
unnamed: J4.2, U1.7 (U/NSin)
unnamed: J4.3, U1.6 (V/PSin)
unnamed: J4.4, U1.5 (W/NCos)
unnamed: J5.1, U1.1 (Data)
unnamed: J5.2, U1.28 (Clock)
unnamed: J6.1, U1.20 (Vout/Tout)
unnamed: J6.2, U1.19 (Refp)
unnamed: J6.3, U1.18 (RefN)
unnamed: J7.1, U1.17 (Mag)
unnamed: J7.2, U1.22 (Zero)
SCL: J1.4, J2.1, U1.24 (SCL)
SDA: J1.3, J2.2, U1.23 (SDA)

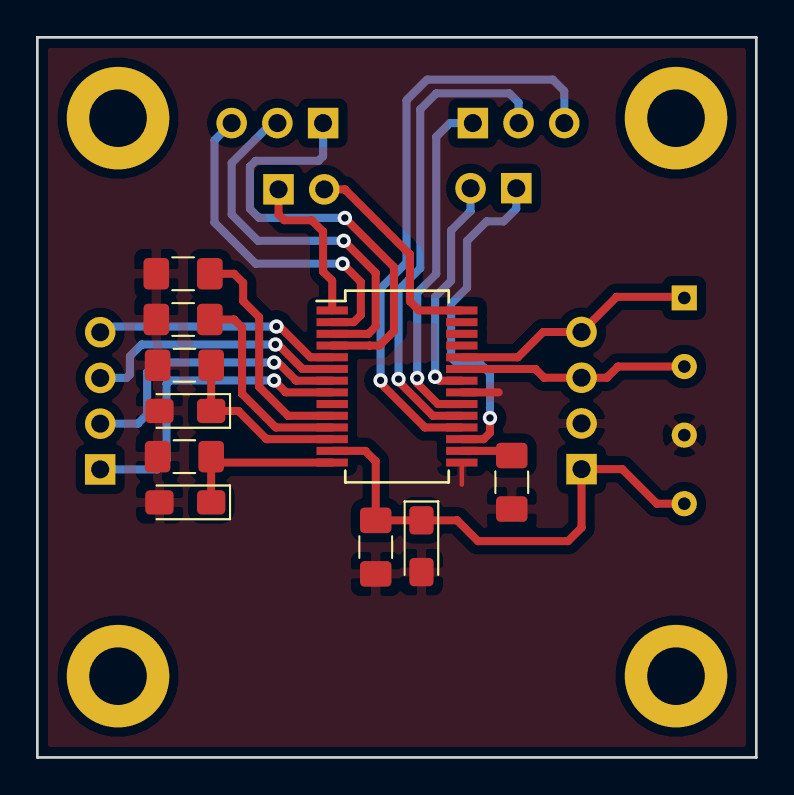
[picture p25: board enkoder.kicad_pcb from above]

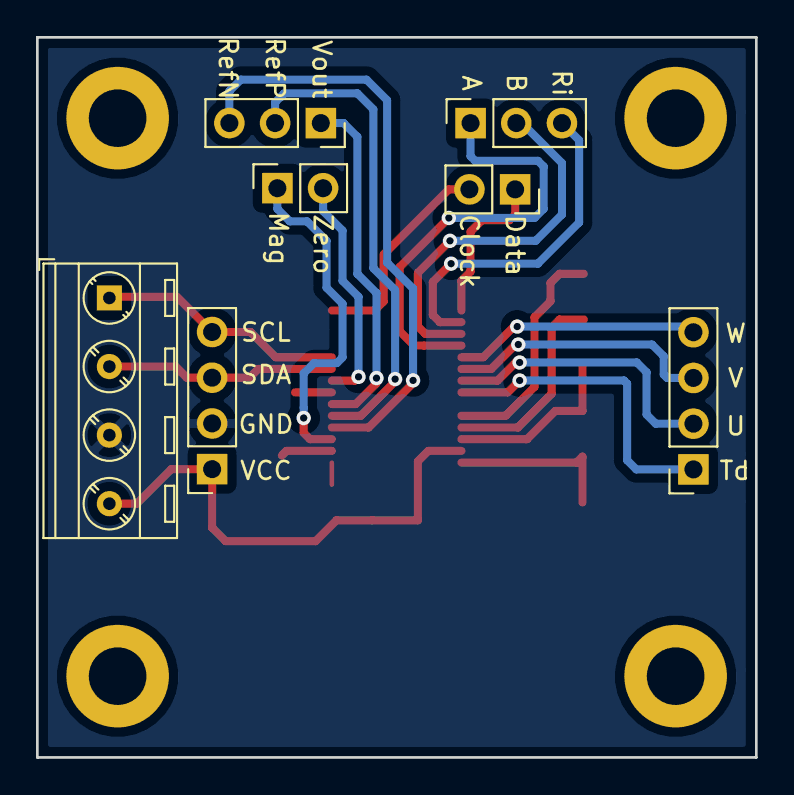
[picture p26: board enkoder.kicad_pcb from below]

Board: 2 copper layers, 39.9 x 40.0 mm, 21 parts (7 on the bottom side), 23 nets.

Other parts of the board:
 : MountingHole_3.2mm_M3_ISO7380_Pad
 #2,  #3,  #4: MountingHole_3.2mm_M3_ISO7380_Pad

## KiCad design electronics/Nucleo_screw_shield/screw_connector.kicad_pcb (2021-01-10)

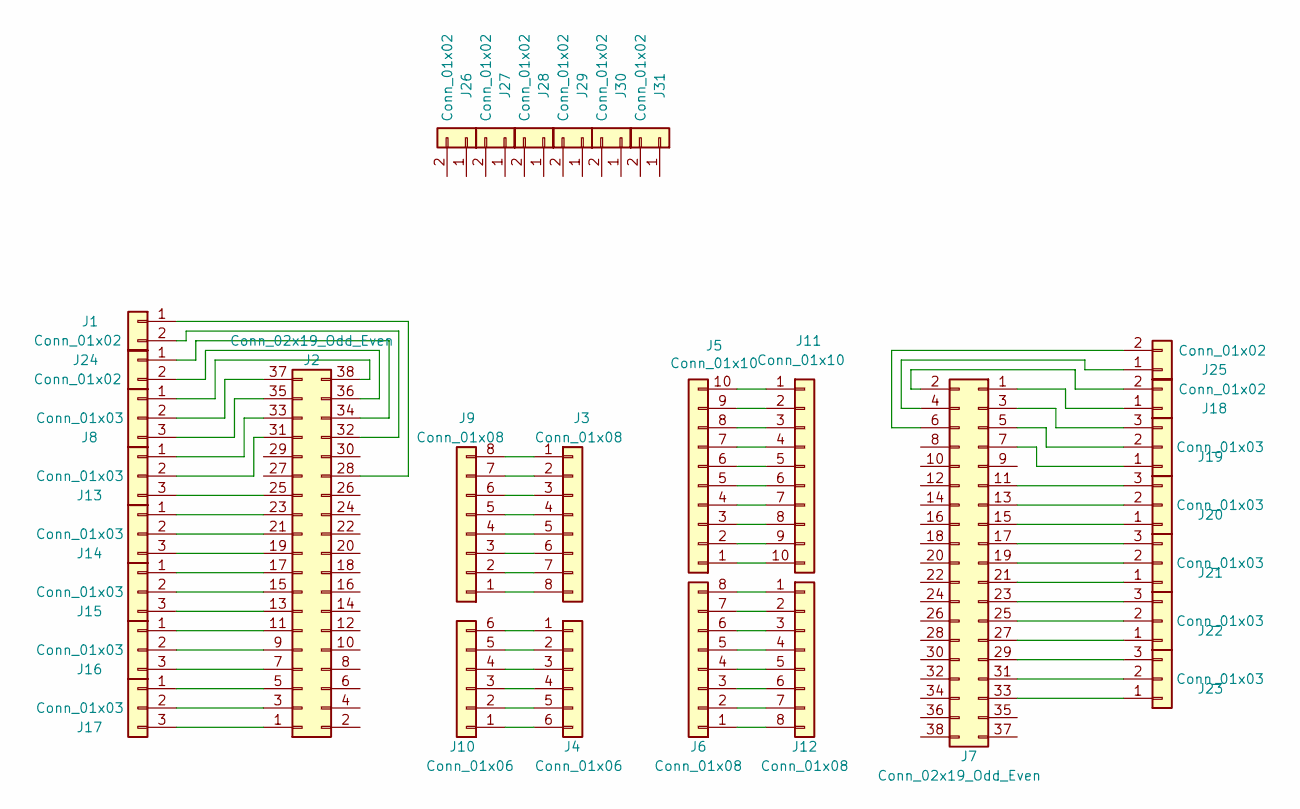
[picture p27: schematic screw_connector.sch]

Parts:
J1, J18, J24, J25, J26, J27, J28, J29, J30, J31: Conn_01x02; TerminalBlock_MetzConnect_Type086_RT03402HBLC_1x02_P3.81mm_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
J2, J7: Conn_02x19_Odd_Even; PinSocket_2x19_P2.54mm_Vertical
J3, J6: Conn_01x08; PinHeader_1x08_P2.54mm_Vertical
J4: Conn_01x06; PinSocket_1x06_P2.54mm_Vertical
J5: Conn_01x10; PinHeader_1x10_P2.54mm_Vertical
J8, J13, J14, J15, J16, J17, J19, J20, J21, J22, J23: Conn_01x03; TerminalBlock_MetzConnect_Type086_RT03403HBLC_1x03_P3.81mm_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
J9, J12: Conn_01x08; PinSocket_1x08_P2.54mm_Vertical
J10: Conn_01x06; PinHeader_1x06_P2.54mm_Vertical
J11: Conn_01x10; PinSocket_1x10_P2.54mm_Vertical

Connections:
unnamed: J1.1, J2.28
unnamed: J1.2, J2.32
unnamed: J2.34, J24.1
unnamed: J2.35, J8.3
unnamed: J2.36, J24.2
unnamed: J2.37, J8.2
unnamed: J2.38, J8.1
unnamed: J3.1, J9.8
unnamed: J3.2, J9.7
unnamed: J3.3, J9.6
unnamed: J3.4, J9.5
unnamed: J3.5, J9.4
unnamed: J3.6, J9.3
unnamed: J3.7, J9.2
unnamed: J3.8, J9.1
unnamed: J4.6, J10.1
unnamed: J4.5, J10.2
unnamed: J4.4, J10.3
unnamed: J4.3, J10.4
unnamed: J4.2, J10.5
unnamed: J4.1, J10.6
unnamed: J5.10, J11.1
unnamed: J5.9, J11.2
unnamed: J5.8, J11.3
unnamed: J5.7, J11.4
unnamed: J5.6, J11.5
unnamed: J5.5, J11.6
unnamed: J5.4, J11.7
unnamed: J5.3, J11.8
unnamed: J5.2, J11.9
unnamed: J5.1, J11.10
unnamed: J6.8, J12.1
unnamed: J6.7, J12.2
unnamed: J6.6, J12.3
unnamed: J6.5, J12.4
unnamed: J6.4, J12.5
unnamed: J6.3, J12.6
unnamed: J6.2, J12.7
unnamed: J6.1, J12.8
unnamed: J2.33, J13.1
unnamed: J2.31, J13.2
unnamed: J2.25, J13.3
unnamed: J2.23, J14.1
unnamed: J2.21, J14.2
unnamed: J2.19, J14.3
unnamed: J2.17, J15.1
unnamed: J2.15, J15.2
unnamed: J2.13, J15.3
unnamed: J2.11, J16.1
unnamed: J2.9, J16.2
unnamed: J2.7, J16.3
unnamed: J2.5, J17.1
unnamed: J2.3, J17.2
unnamed: J2.1, J17.3
unnamed: J7.1, J18.1
unnamed: J7.2, J18.2
unnamed: J7.7, J19.1
unnamed: J7.5, J19.2
unnamed: J7.3, J19.3
unnamed: J7.15, J20.1
unnamed: J7.13, J20.2
unnamed: J7.11, J20.3
unnamed: J7.21, J21.1
unnamed: J7.19, J21.2
unnamed: J7.17, J21.3
unnamed: J7.27, J22.1
unnamed: J7.25, J22.2
unnamed: J7.23, J22.3
unnamed: J7.33, J23.1
unnamed: J7.31, J23.2
unnamed: J7.29, J23.3
unnamed: J7.4, J25.1
unnamed: J7.6, J25.2

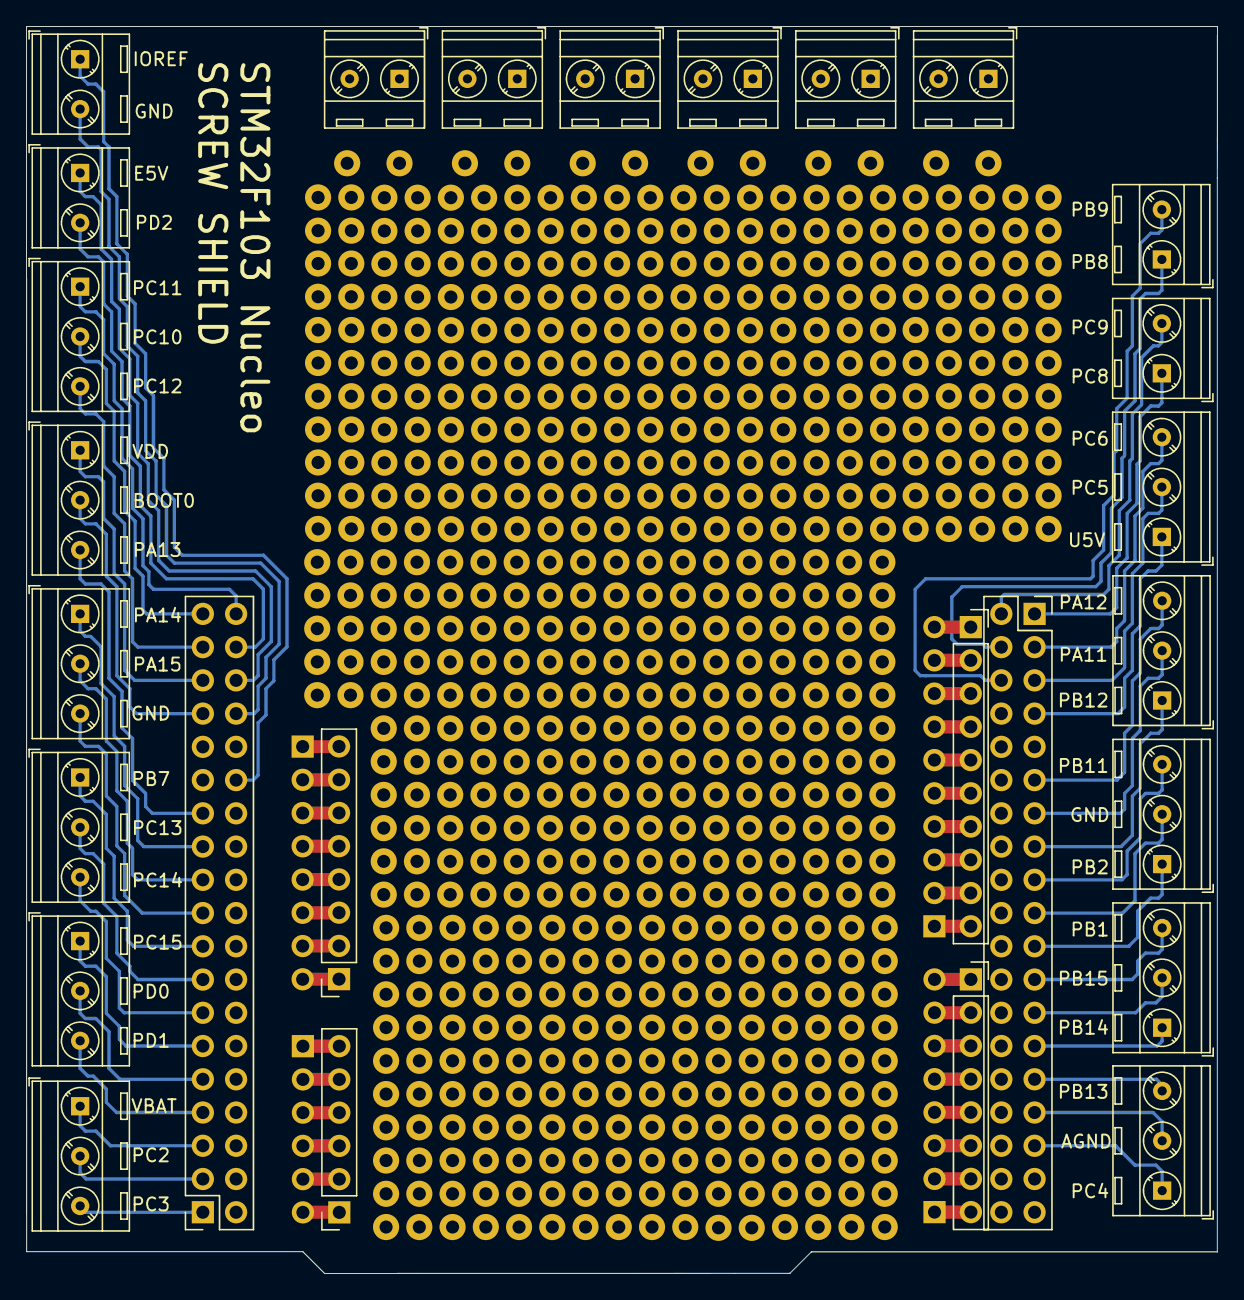
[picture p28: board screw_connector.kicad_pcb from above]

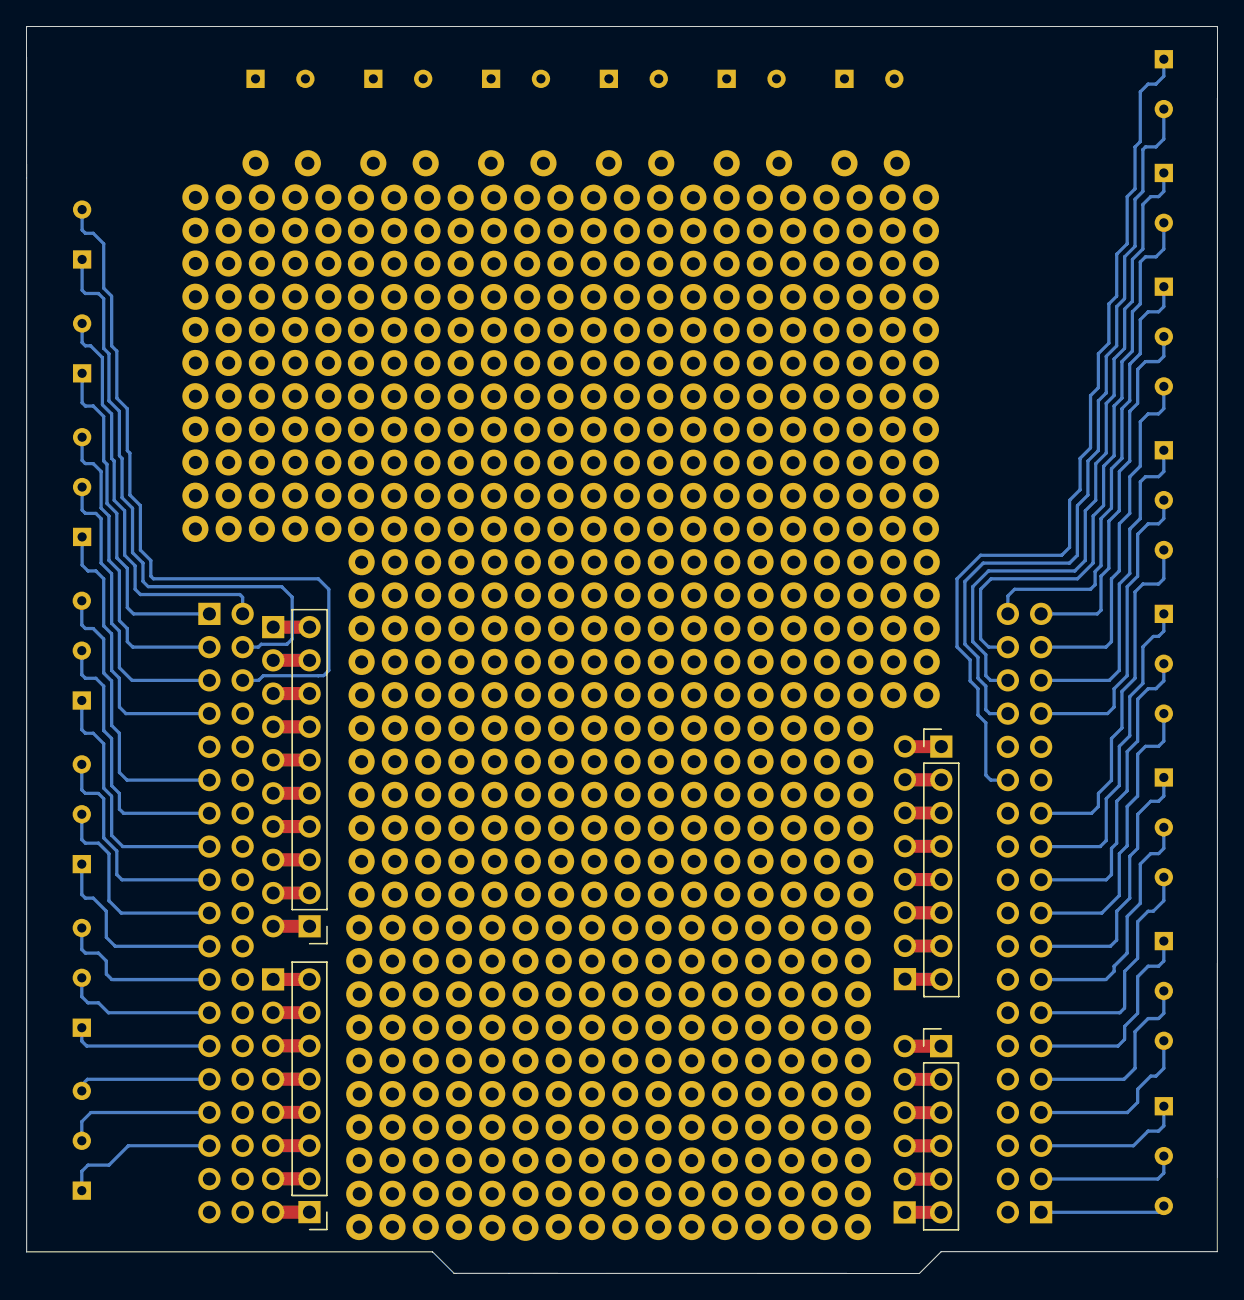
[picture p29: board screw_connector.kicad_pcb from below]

Board: 2 copper layers, 91.0 x 95.3 mm, 31 parts (4 on the bottom side), 73 nets.

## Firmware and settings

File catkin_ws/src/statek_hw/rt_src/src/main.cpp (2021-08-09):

#include "../include/config.hpp"

#include <Arduino.h>
#include <Wire.h>
#include <MPU9250.h>
#include "../include/motor_controller.hpp"
#include "../include/odometry.hpp"

#include "../include/ros.hpp"

#include "../lib/ros_lib/statek_hw/Velocity.h"
#include "../lib/ros_lib/statek_hw/Encoder.h"
#include "../lib/ros_lib/statek_hw/RunVelocityTest.h"
#include "../lib/ros_lib/statek_hw/SetMotorParams.h"
#include "../lib/ros_lib/statek_hw/RunModelIdentification.h"
#include "../lib/ros_lib/std_srvs/Trigger.h"

#include "../lib/ros_lib/statek_hw/SetImuParams.h"
#include "../lib/ros_lib/statek_hw/RunImuCalibration.h"
#include "../lib/ros_lib/sensor_msgs/Imu.h"

#include "../lib/ros_lib/statek_hw/SetOdomParams.h"
#include "../lib/ros_lib/nav_msgs/Odometry.h"
#include "../lib/ros_lib/tf/transform_broadcaster.h"
#include "../lib/ros_lib/tf/tf.h"

bool imuReady = false;           //!< Whether IMU is ready.
float imuMagDecRad = 0;

/**
 * @brief Arduino's setup function.
 * 
 * Sets all ROS services and prepares all hardware.
 */
void setup();

/**
 * @brief Arduino's loop function.
 */
void loop();

/**
 * @brief Update all the stuff!
 * 
 * Updates ROS, hardware and SAFETY.
 * @param rosPublish Whether allow ROS to publish data. Should be set to false when called from some service.
 */
void update(bool rosPublish = true);

/**
 * @brief Try update ROS.
 * @param publish Whether ROS is allowed to publish data.
 * @return True if updated.
 */
bool tryUpdateROS(bool publish = true);

/**
 * @brief Update ROS stuff.
 * @param publish Whether ROS is allowed to publish data.
 */
void updateROS(bool publish = true);

/**
 * @brief Whether hardware stuff is ready, all params loaded etc.
 * @return True if ready.
 */
bool hardwareReady();

/**
 * @brief Try update all of the hardware.
 * @return True if hardware COULD update. This does not mean that the hardware updated.
 */
bool tryUpdateHardware();

/**
 * @brief Run all safety measurements.
 */
void SAFETY();

// Callbacks for subscribers.
/**
 * @brief Called when ROS serial received new setpoint values from master.
 * @param setpoints Setpoints for both wheels.
 */
void setpointsSubscriberCallback(const statek_hw::Velocity &setpoints);

// Callbacks for services.
/**
 * @brief Called when user wants to check max velocity. Performs max velocity test for given time.
 * @param req Request structure.
 * @param res Response structure.
 */
void maxVelocityTestServiceCallback(const statek_hw::RunVelocityTestRequest &req, statek_hw::RunVelocityTestResponse &res);

/**
 * @brief Called when user wants to identify some motor's dynamics. Collects 100 velocity step response samples for some time.
 * @param mot Motor to perform identification on.
 * @param req Request structure.
 * @param res Response structure.
 */
void stepResponseIdentificationServiceCallback(MotorController &mot, const statek_hw::RunModelIdentificationRequest &req, statek_hw::RunModelIdentificationResponse &res);

/**
 * @brief Perform step response identification on left motor.
 * @param req Request structure.
 * @param res Response structure.
 */
void leftMotorStepResponseIdentificationServiceCallback(const statek_hw::RunModelIdentificationRequest &req, statek_hw::RunModelIdentificationResponse &res);

/**
 * @brief Perform step response identification on right motor.
 * @param req Request structure.
 * @param res Response structure.
 */
void rightMotorStepResponseIdentificationServiceCallback(const statek_hw::RunModelIdentificationRequest &req, statek_hw::RunModelIdentificationResponse &res);

/**
 * @brief Called when user wants to switch to open loop control. Sets open loop control.
 * @param req Request structure.
 * @param res Response structure.
 */
void setDirectControlServiceCallback(const std_srvs::TriggerRequest &req, std_srvs::TriggerResponse &res);

/**
 * @brief Called when user wants to switch to closed loop control. Sets closed loop control.
 * @param req Request structure.
 * @param res Response structure.
 */
void setClosedLoopControlServiceCallback(const std_srvs::TriggerRequest &req, std_srvs::TriggerResponse &res);

/**
 * @brief Called when user wants to set left motors params. Sets left motor's params.
 * @param req Request structure.
 * @param res Response structure.
 */
void setLeftMotorParamsCallback(const statek_hw::SetMotorParamsRequest &req, statek_hw::SetMotorParamsResponse &res);

/**
 * @brief Called when user wants to set right motors params. Sets right motor's params.
 * @param req Request structure.
 * @param res Response structure.
 */
void setRightMotorParamsCallback(const statek_hw::SetMotorParamsRequest &req, statek_hw::SetMotorParamsResponse &res);

/**
 * @brief Called when user wants to calibrate IMU. Performs IMU calibration.
 * 
 * This function requires that motors have some non zero max velocity!
 * @param req Request structure.
 * @param res Response structure.
 */
void imuCalibrationServiceCallback(const statek_hw::RunImuCalibrationRequest &req, statek_hw::RunImuCalibrationResponse &res);

/**
 * @brief Called when user wants to set IMU's parameters. Sets IMU's parameters.
 * @param req Request structure.
 * @param res Response structure.
 */
void setImuParamsServiceCallback(const statek_hw::SetImuParamsRequest &req, statek_hw::SetImuParamsResponse &res);

/**
 * @brief Called when user wants to set odom's parameters. Sets odom's parameters.
 * @param req Request structure.
 * @param res Response structure.
 */
void setOdomParamsCallback(const statek_hw::SetOdomParamsRequest &req, statek_hw::SetOdomParamsResponse &res);

// Publisher functions
/**
 * @brief Try to publish encoder's state. Can fail if not enough time has passed since last update.
 * @return True on success.
 */
bool tryPublishEncoders();

/**
 * @brief Publish encoder's state to ROS.
 */
void publishEncoders();

/**
 * @brief Try to publish IMU's state. Can fail if not enough time has passed since last update.
 * @return True on success.
 */
bool tryPublishIMU();

/**
 * @brief Publish IMU's state to ROS.
 */
void publishIMU();

/**
 * @brief Try to publish odom's state. Can fail if not enough time has passed since last update.
 * @return True on success.
 */
bool tryPublishOdom();

/**
 * @brief Publish odom's state to ROS along with tf.
 */
void publishOdom();

// Helper functions
/**
 * @brief Force some velocities on both motors and wait for them to accelerate to these velocities.
 * 
 * This functions requires max velocity on both motors to be greater than zero.
 * This function should be called by services not tied to the motors that require some motor movement (i.e mag calibration).
 * @param leftNormalized Value between -1 (max speed reverse) and 1 (max speed forward).
 * @param rightNormalized Value between -1 (max speed reverse) and 1 (max speed forward).
 * @param time How long to wait for motors to accelerate to given speed.
 * @return True on success.
 */
bool forceWheelMovement(float leftNormalized, float rightNormalized, unsigned long time);

// SAFETY functions and variables
bool SAFETY_serviceInProgress = false;          //!< Should be set to true during service callback and to false at the end of it. Every service callback should firstly check whether this flag is set to true and if so then fail.
bool SAFETY_stopMotorsFlag = false;             //!< Any function related to motor movement should reset this flag as frequent as possible. If not, safety measurements will stop the motors.
int SAFETY_motorsCommunicationFlowSupervisor(); //!< Check whether there is active communication flow between ROS master and this uC.

// ROS stuff
ros::NodeHandle nh; //!< Manage all ROS stuff.

statek_hw::Velocity setpoints; //!< Message for setpoints.
ros::Subscriber<statek_hw::Velocity>
    setpointsSubscriber(VELOCITY_SETPOINTS_TOPIC, &setpointsSubscriberCallback); //!< Setpoint subscriber object.

ros::ServiceServer<statek_hw::RunVelocityTestRequest, statek_hw::RunVelocityTestResponse>
    maxVelocityTestService(VELOCITY_TEST_SERVICE, &maxVelocityTestServiceCallback); //!< Max velocity test service object.

ros::ServiceServer<statek_hw::RunModelIdentificationRequest, statek_hw::RunModelIdentificationResponse>
    leftMotorStepResponseIdentificationService(LEFT_MOTOR_STEP_RESPONSE_IDENTIFICATION_SERVICE, &leftMotorStepResponseIdentificationServiceCallback); //!< Step identification for left motor service object.

ros::ServiceServer<statek_hw::RunModelIdentificationRequest, statek_hw::RunModelIdentificationResponse>
    rightMotorStepResponseIdentificationService(RIGHT_MOTOR_STEP_RESPONSE_IDENTIFICATION_SERVICE, &rightMotorStepResponseIdentificationServiceCallback); //!< Step identification for right motor service object.

ros::ServiceServer<std_srvs::TriggerRequest, std_srvs::TriggerResponse>
    directControlService(DIRECT_CONTROL_SERVICE, &setDirectControlServiceCallback); //!< Direct control service object.

ros::ServiceServer<std_srvs::TriggerRequest, std_srvs::TriggerResponse>
    closedLoopControlService(PID_CONTROL_SERVICE, &setClosedLoopControlServiceCallback); //!< PID control service object.

ros::ServiceServer<statek_hw::SetMotorParamsRequest, statek_hw::SetMotorParamsResponse>
    setLeftMotorParamsService(LEFT_MOTOR_PARAM_SERVICE, &setLeftMotorParamsCallback); //!< Set left motor params service object.

ros::ServiceServer<statek_hw::SetMotorParamsRequest, statek_hw::SetMotorParamsResponse>
    setrightMotorParamsService(RIGHT_MOTOR_PARAM_SERVICE, &setRightMotorParamsCallback); //!< Set right motor param service object.

ros::ServiceServer<statek_hw::RunImuCalibrationRequest, statek_hw::RunImuCalibrationResponse>
    imuCalibrationService(IMU_CALIBRATION_SERVICE, &imuCalibrationServiceCallback); //!< IMU calibration service object.

ros::ServiceServer<statek_hw::SetImuParamsRequest, statek_hw::SetImuParamsResponse>
    setImuParamsService(IMU_PARAM_SERVICE, &setImuParamsServiceCallback); //!< Set IMU params service object.

ros::ServiceServer<statek_hw::SetOdomParamsRequest, statek_hw::SetOdomParamsResponse>
    setOdomParamsService(ODOM_PARAM_SERVICE, &setOdomParamsCallback); //!< Set odom params service object.

statek_hw::Encoder leftEncoderMsg;                                              //!< Message for left encoder publisher.
ros::Publisher leftEncoderPublisher(LEFT_MOTOR_ENCODER_TOPIC, &leftEncoderMsg); //!< Left encoder publisher object.

statek_hw::Encoder rightEncoderMsg;                                                //!< Message for right encoder publisher.
ros::Publisher rightEncoderPublisher(RIGHT_MOTOR_ENCODER_TOPIC, &rightEncoderMsg); //!< Right encoder publisher object.

sensor_msgs::Imu imuMsg;                         //!< Message for IMU publisher.
ros::Publisher imuPublisher(IMU_TOPIC, &imuMsg); //!< IMU publisher object.

nav_msgs::Odometry odomMsg;                         //!< Message for odom publisher.
ros::Publisher odomPublisher(ODOM_TOPIC, &odomMsg); //!< Odom publisher object.
geometry_msgs::TransformStamped odomTrans;          //!< Odom transform message.
tf::TransformBroadcaster odomBroadcaster;           //!< Odom transform broadcaster.

MotorController leftMotor(LEFT_MOTOR_GPIO, LEFT_MOTOR_ENCODER_I2C_ADDRESS, true); //!< Left motor control loop.
MotorController rightMotor(RIGHT_MOTOR_GPIO, RIGHT_MOTOR_ENCODER_I2C_ADDRESS);    //!< Right motor control loop.

MPU9250 imu; //!< IMU.

Odometry odom(leftMotor, rightMotor); //!< Odometry.

void setup()
{
    // Init ROS stuff.
    //nh.setSpinTimeout(1);
    nh.initNode();
    odomBroadcaster.init(nh);

    nh.subscribe(setpointsSubscriber);
    nh.advertiseService(maxVelocityTestService);
    nh.advertiseService(leftMotorStepResponseIdentificationService);
    nh.advertiseService(rightMotorStepResponseIdentificationService);
    nh.advertiseService(directControlService);
    nh.advertiseService(closedLoopControlService);
    nh.advertiseService(setLeftMotorParamsService);
    nh.advertiseService(setrightMotorParamsService);
    nh.advertise(rightEncoderPublisher);
    nh.advertise(leftEncoderPublisher);

    nh.advertiseService(imuCalibrationService);
    nh.advertiseService(setImuParamsService);
    nh.advertise(imuPublisher);

    nh.advertiseService(setOdomParamsService);
    nh.advertise(odomPublisher);

    // Add some static message values here.
    leftEncoderMsg.header.frame_id = LEFT_MOTOR_TF_LINK;
    rightEncoderMsg.header.frame_id = RIGHT_MOTOR_TF_LINK;

    imuMsg.header.frame_id = IMU_TF_LINK;

    odomMsg.header.frame_id = ODOM_TF_LINK;
    odomMsg.child_frame_id = ODOM_CHILD_LINK;
    odomTrans.header.frame_id = ODOM_TF_LINK;
    odomTrans.child_frame_id = ODOM_CHILD_LINK;

    // Init I2C.
    Wire.begin();

    // Init sensors and actuators.
    leftMotor.start();
    rightMotor.start();
    odom.start();

    MPU9250Setting settings;
    settings.accel_fs_sel = ACCEL_FS_SEL::A2G;
    settings.gyro_fs_sel = GYRO_FS_SEL::G250DPS;
    settings.mag_output_bits = MAG_OUTPUT_BITS::M16BITS;
    settings.fifo_sample_rate = FIFO_SAMPLE_RATE::SMPL_125HZ;
    imu.selectFilter(QuatFilterSel::MADGWICK);
    imu.setup(IMU_I2C_ADDRESS, settings);
}

void loop()
{
    update();
}

void update(bool rosPublish)
{
    tryUpdateROS(rosPublish);
    tryUpdateHardware();
    SAFETY();
}

bool tryUpdateROS(bool publish)
{
    static unsigned long previousRosUpdateTime = millis();

    unsigned long now = millis();
    // Handle clock overflow.
    if ((now >= previousRosUpdateTime))
    {
        // Check if some time passed so we can update ROS.
        if (now - previousRosUpdateTime >= 20)
        {
            updateROS(publish);
            previousRosUpdateTime = now;
            return true;
        }
    }
    else
    {
        previousRosUpdateTime = now;
    }
    return false;
}

void updateROS(bool publish)
{
    nh.spinOnce();
    if (publish && hardwareReady())
    {
        tryPublishEncoders();
        tryPublishIMU();
        tryPublishOdom();
    }
}

bool hardwareReady()
{
    bool ready = true;
    ready = ready && leftMotor.isReady() && rightMotor.isReady() && odom.isReady();
    ready = ready && imu.isConnected() && imuReady;
    return ready;
}

bool tryUpdateHardware()
{
    if (!hardwareReady())
        return false;

    leftMotor.tryUpdate();
    rightMotor.tryUpdate();
    if (imuReady)
        imu.update();
    odom.tryUpdate();

    return true;
}

void SAFETY()
{
    SAFETY_motorsCommunicationFlowSupervisor();
}

// Callbacks for subscribers.
void setpointsSubscriberCallback(const statek_hw::Velocity &setpoints)
{
    // Don't disturb the service.
    if (SAFETY_serviceInProgress)
    {
        return;
    }

    rightMotor.requestVelocity(setpoints.right);
    leftMotor.requestVelocity(setpoints.left);
    SAFETY_stopMotorsFlag = false; // A message arrived so don's stop the motors.
}

// Callbacks for services.
void maxVelocityTestServiceCallback(const statek_hw::RunVelocityTestRequest &req, statek_hw::RunVelocityTestResponse &res)
{
    // Don't run the test when another callback is doing stuff.
    if (SAFETY_serviceInProgress)
    {
        res.success = false;
        return;
    }

    SAFETY_serviceInProgress = true;

    MotorController::ControlMode previousMode = rightMotor.getControlMode(); // Restore previous mode after test.

    // Begin the test.
    rightMotor.setControlMode(MotorController::ControlMode::MAX_VELOCITY_TEST);
    leftMotor.setControlMode(MotorController::ControlMode::MAX_VELOCITY_TEST);

    // Let it do it's job for given time.
    unsigned long start = millis();
    unsigned long now = millis();
    bool overflowFlag = false;
    while (now - start < req.time_ms)
    {
        now = millis();
        // Clock overflow
        // Really rare situation.
        // So just mark test as failed.
        if (now < start)
        {
            overflowFlag = true;
            break;
        }

        SAFETY_stopMotorsFlag = false; // Also reset this flag so motor's won't stop due to safety reasons.
        update(false);                 // Keep other parts of the system alive.
    }

    // Restore previous mode.
    rightMotor.setControlMode(previousMode);
    leftMotor.setControlMode(previousMode);

    // Treat mean velocity as maximum velocity to reject noise etc.
    float rightMaxVel = rightMotor.getMaxVelocityTestResult();
    float leftMaxVel = leftMotor.getMaxVelocityTestResult();

    // Set lower value as max possible velocity so both motors will be able to achieve it.
    float maxVel = rightMaxVel;
    if (leftMaxVel < rightMaxVel)
        maxVel = leftMaxVel;

    // Finally, respond to the caller.
    res.success = !overflowFlag;
    res.velocity = maxVel;

    SAFETY_serviceInProgress = false;
}

void stepResponseIdentificationServiceCallback(MotorController &mot, const statek_hw::RunModelIdentificationRequest &req, statek_hw::RunModelIdentificationResponse &res)
{
    const uint8_t numSamples = 100;

    // Don't run the test when another callback is doing stuff.
    if (SAFETY_serviceInProgress)
    {
        res.success = false;
        return;
    }

    SAFETY_serviceInProgress = true;

    res.sampling_time = (req.identification_time_ms / 1000.0) / (float)numSamples;
    unsigned int sampleTime = res.sampling_time * 1000;
    bool overflowFlag = false;

    MotorController::ControlMode previousMode = mot.getControlMode();

    // Perform identification.
    mot.requestVelocity(0);
    mot.setControlMode(MotorController::ControlMode::STEP_IDENTIFICATION);

    for (uint8_t i = 0; i < numSamples; i++)
    {
        unsigned long start = millis();
        unsigned long now = start;

        // Wait for next sample.
        while (now - start < sampleTime)
        {
            now = millis();
            // Clock overflow.
            if (now < start)
            {
                overflowFlag = true;
                break;
            }

            SAFETY_stopMotorsFlag = false; // Also reset this flag so motor's won't stop due to safety reasons.
            update(false);                 // Keep other parts of the system alive.
        }

        // Get the sample.
        res.samples[i] = mot.getLatestEncoderState().velocity;
    }

    // Restore previous control mode.
    mot.setControlMode(previousMode);

    res.success = !overflowFlag;

    SAFETY_serviceInProgress = false;
}

void leftMotorStepResponseIdentificationServiceCallback(const statek_hw::RunModelIdentificationRequest &req, statek_hw::RunModelIdentificationResponse &res)
{
    stepResponseIdentificationServiceCallback(leftMotor, req, res);
}

void rightMotorStepResponseIdentificationServiceCallback(const statek_hw::RunModelIdentificationRequest &req, statek_hw::RunModelIdentificationResponse &res)
{
    stepResponseIdentificationServiceCallback(rightMotor, req, res);
}

void setDirectControlServiceCallback(const std_srvs::TriggerRequest &req, std_srvs::TriggerResponse &res)
{
    // Don't run the test when another callback is doing stuff.
    if (SAFETY_serviceInProgress)
    {
        res.success = false;
        return;
    }

    SAFETY_serviceInProgress = true;

    rightMotor.setControlMode(MotorController::ControlMode::DIRECT);
    leftMotor.setControlMode(MotorController::ControlMode::DIRECT);

    res.success = true;

    SAFETY_serviceInProgress = false;
}

void setClosedLoopControlServiceCallback(const std_srvs::TriggerRequest &req, std_srvs::TriggerResponse &res)
{
    if (SAFETY_serviceInProgress)
    {
        res.success = false;
        return;
    }
    SAFETY_serviceInProgress = true;

    rightMotor.setControlMode(MotorController::ControlMode::PID_CONTROL);
    leftMotor.setControlMode(MotorController::ControlMode::PID_CONTROL);

    res.success = true;

    SAFETY_serviceInProgress = false;
}

void setLeftMotorParamsCallback(const statek_hw::SetMotorParamsRequest &req, statek_hw::SetMotorParamsResponse &res)
{
    static bool alreadySet = false;
    if (alreadySet)
    {
        res.success = false;
        return;
    }

    // Don't run the test when another callback is doing stuff.
    if (SAFETY_serviceInProgress)
    {
        res.success = false;
        return;
    }

    SAFETY_serviceInProgress = true;

    MotorController::ControlParams params = {
        req.kp, req.ki, req.kd, req.smoothing_factor, req.loop_update_rate_ms, req.wheel_max_angular_velocity};

    leftMotor.setMotorParams(params);

    alreadySet = true;

    res.success = true;

    SAFETY_serviceInProgress = false;
}

void setRightMotorParamsCallback(const statek_hw::SetMotorParamsRequest &req, statek_hw::SetMotorParamsResponse &res)
{
    static bool alreadySet = false;
    if (alreadySet)
    {
        res.success = false;
        return;
    }

    // Don't run the test when another callback is doing stuff.
    if (SAFETY_serviceInProgress)
    {
        res.success = false;
        return;
    }
    SAFETY_serviceInProgress = true;

    MotorController::ControlParams params = {
        req.kp, req.ki, req.kd, req.smoothing_factor, req.loop_update_rate_ms, req.wheel_max_angular_velocity};

    rightMotor.setMotorParams(params);

    alreadySet = true;

    res.success = true;

    SAFETY_serviceInProgress = false;
}
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

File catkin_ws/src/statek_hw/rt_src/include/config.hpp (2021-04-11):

#pragma once

/*
The only file you should touch.

* Topics musn't have namespace.
* Tf links must have namespace.
*/

#define D_SDA PB9
#define D_SCL PB8

#define RIGHT_MOTOR_GPIO   \
    {                      \
        PA0, PA8, PA9, PB4 \
    } // Enable, clockwise, counter clockwise, pwm.
#define RIGHT_MOTOR_ENCODER_I2C_ADDRESS 0x1E
#define RIGHT_MOTOR_ENCODER_TOPIC "motors/right/encoder"
#define RIGHT_MOTOR_TF_LINK "statek/wheels/right_front_link"
#define RIGHT_MOTOR_PARAM_SERVICE "motors/right/set_params"
#define RIGHT_MOTOR_STEP_RESPONSE_IDENTIFICATION_SERVICE "motors/right/step_response_identification"

#define LEFT_MOTOR_GPIO     \
    {                       \
        PA1, PB5, PC7, PB10 \
    }
#define LEFT_MOTOR_ENCODER_I2C_ADDRESS 0x3C
#define LEFT_MOTOR_ENCODER_TOPIC "motors/left/encoder"
#define LEFT_MOTOR_TF_LINK "statek/wheels/left_front_link"
#define LEFT_MOTOR_PARAM_SERVICE "motors/left/set_params"
#define LEFT_MOTOR_STEP_RESPONSE_IDENTIFICATION_SERVICE "motors/left/step_response_identification"

#define VELOCITY_SETPOINTS_TOPIC "motors/vel_cmd"

#define VELOCITY_TEST_SERVICE "motors/max_velocity_test"
#define DIRECT_CONTROL_SERVICE "motors/set_direct_control"
#define PID_CONTROL_SERVICE "motors/set_pid_control"

#define IMU_I2C_ADDRESS 0x68
#define IMU_TOPIC "imu"
#define IMU_TF_LINK "statek/imu/imu_link"
#define IMU_CALIBRATION_SERVICE "imu/calibrate"
#define IMU_PARAM_SERVICE "imu/set_params"

#define ODOM_TOPIC "odom"
#define ODOM_TF_LINK "statek/odom/odom_link"
#define ODOM_CHILD_LINK "statek/base_footprint"
#define ODOM_PARAM_SERVICE "odom/set_params"

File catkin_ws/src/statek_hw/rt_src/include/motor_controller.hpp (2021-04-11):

#pragma once

#include <Arduino.h>
#include <Wire.h>

#include "../include/motor.hpp"
#include "../include/am4096.hpp"
#include "../include/pid.hpp"
#include "../include/low_pass_filter.hpp"

class MotorController
{
public:
    /**
     * @brief Contains error codes that can be returned from MotorController::tryUpdate()
     */
    enum FailCode
    {
        CONTROL_UPDATED,  //!< Success.
        LOOP_RATE_ZERO,   //!< User didn't provided loop rate.
        UPDATE_NOT_READY, //!< Not enough time has passed since previous update.
        ENCODER_FAILURE,  //!< Something gone wrong with the encoder.
        MOTOR_NOT_READY   //!< Ready flag is not set.
    };

    /**
     * @brief One of the possible control modes.
     */
    enum ControlMode
    {
        MAX_VELOCITY_TEST,   //!< Spin with max CV and compute average speed.
        STEP_IDENTIFICATION, //!< Just spin with max CV.
        DIRECT,              //!< Open loop control.
        PID_CONTROL         //!< Closed loop control.
    };

    /**
     * @brief Struct with encoder's state.
     */
    struct EncoderState
    {
        float position;
        float velocity;
        float acceleration;
    };

    /**
     * @brief Params that can be set to this object.
     */
    struct ControlParams
    {
        float kp;
        float ki;
        float kd;
        float smoothingFactor;       //!< Between 0 and 1.
        unsigned int loopUpdateRate; //!< How fast the loop should update in milliseconds.
        float maxVelocity;           //!< In radians per second.
    };

private:
    bool ready = false; //!< Whether the loop should start updating.

    // Hardware
    Motor motor;                 //!< Motor to control.
    AM4096 encoder;              //!< Encoder attached to the motor somehow.
    bool reverseEncoder = false; //!< Whether read encoder as 2PI - reading (if true) or just as reading (if false).

    // For max velocity test control mode.
    float averageVelocity = 0;                   //!< Average velocity computed during MAX_VELOCITY_TEST.
    unsigned int movingAverageSampleTracker = 0; //!< Helper for MotorController::averageVelocity.

    // Control system stuff.
    unsigned long previousUpdateTime = 0;               //!< Timestamp of previous update.
    float setpoint = 0;                                 //!< Setpoint in radians per second.
    float maxVelocity = 0;                              //!< Max possible setpoint.
    unsigned int loopUpdateRate = 30;                   //!< How fast the loop should update in milliseconds.
    ControlMode controlMode = ControlMode::PID_CONTROL; //!< Current control mode.
    LowPassFilter fakeInertia;                          //!< To smooth out the movement of the motor.
    PIDController pid;                                  //!< PID controller.
    EncoderState latestEncoderState;                    //!< Used to compute some stuff in MotorController::update() and to be accessed by anyone interesed.

    /**
     * @brief Read encoder hardware and fill MotorController::EncoderState with readings and estimations.
     * @param ok Set to true on success, false otherwise.
     * @return State of the encoder on success.
     */
    EncoderState getCurrentEncoderState(bool &ok) const;

    /**
     * @brief Get control value that will be written to the motor.
     * This value depends on the control mode but is guaranteed to be between -1 and 1.
     * @param currentEncoderState Current encoder state.
     * @return Control value.
     */
    float getControlValue(const EncoderState &currentEncoderState);

    /**
     * @brief Update control loop.
     * In case this function fails, the setpoint will be set to 0 for safety reasons.
     * @return True if update suceeded. False if there was hardware failure.
     */
    bool update();

    /**
     * @brief Saturate value between min and max.
     * @param minVal Minimum possible value.
     * @param maxVal Maximum possible value
     * @param val Value to saturate.
     * @return Saturated value.
     */
    static float saturate(float minVal, float maxVal, float val);

public:
    /**
     * @brief Class constructor.
     * @param motorGpio GPIO to control the motor.
     * @param encoderAddr I2C address of the encoder.
     * @param _reverseEncoder Whether to reverse encoder reading.
     * @param encoderI2c I2C device to read encoder state on.
     */
    MotorController(const Motor::Gpio &motorGpio, uint8_t encoderAddr, bool _reverseEncoder = false, TwoWire &encoderI2c = Wire);

    /**
     * @brief Start the controller. This will set up some variables.
     */
    void start();

    /**
     * @brief Whether the controller is ready. i.e has all necessary parameters loaded througs MotorController::setMotorParams.
     * @return True if ready.
     */
    bool isReady() const;

    /**
     * @brief Try update the control loop. Can fail if not enough time has passed since last update or due to hardware failure.
     * @return MotorController::FailCode indicating what happened during this function.
     */
    FailCode tryUpdate();

    /**
     * @brief Set setpoint to the controller.
     * @param vel Velocity to request.
     */
    void requestVelocity(float vel);

    /**
     * @brief Set all motor params.
     * 
     * Floats with negative value are ignored.
     * This function sets ready flag if maxVelocity and loopUpdateRate are bigger than 0.
     * Otherwise it resets this flag.
     * @param params Params to set.
     */
    void setMotorParams(const ControlParams &params);

    /**
     * @brief Set control mode.
     * @param cm Control mode to set.
     */
    void setControlMode(ControlMode cm);

    /**
     * @brief Get current setpoint.
     * @return Current setpoint.
     */
    float getRequestedVelocity() const;

    /**
     * @brief Get current control mode.
     * @return current control mode.
     */
    ControlMode getControlMode() const;

    /**
     * @brief Get encoder state from previous update.
     * @return Encoder state.
     */
    EncoderState getLatestEncoderState() const;

    /**
     * @brief Get max possible velocity in radians per second.
     * @return Max possible velocity.
     */
    float getMaxVelocity() const;

    /**
     * @brief Returns average velocity found during MAX_VELOCITY_TEST.
     * @return Result of MAX_VELOCITY_TEST.
     */
    float getMaxVelocityTestResult() const;
};

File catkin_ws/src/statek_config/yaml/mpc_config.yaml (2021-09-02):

goal_area: 1 # Radius around goal point that will count as a goal.
solver_options: "Integer print_level 0\nSparse true forward\nSparse true reverse\nNumeric max_cpu_time 0.7\n"

# Horizon parameters.
# _forward will be used when orientation error is 0.
# _rotate will be used when absolute orientation error equals to pi.
# values in between will be interpolated.
horizon_duration_forward: 15
horizon_sampling_forward: 0.5
horizon_duration_rotate: 3
horizon_sampling_rotate: 0.1

pose_weight: 10
cte_weight: 30
oe_weight: 700000

linear_velocity_weight: 0
angular_velocity_weight: 0

linear_velocity_delta_weight: 3
angular_velocity_delta_weight: 0.1

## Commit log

2020-12-22 Reorganize CAD files
    [base.ipt, chassis.ipt, damping_system_housing_connector.ipt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]
2020-12-22 Add tf, rviz, hw packages. Add lidar
2020-12-24 Add mesh to statek_rviz
    [statek.urdf]
2020-12-24 Edit assembly.iam
2020-12-24 Work on launch files, add xyz args to spawn_statek.launch
    [statek.urdf]
2020-12-24 Change from sdf to urdf
    [model.sdf, statek.urdf]
2020-12-25 Edit dae urdf model
2020-12-25 Finish screw shield
    [screw_connector.kicad_pcb]
2020-12-25 Finish AM4096 encoder board
    [enkoder.kicad_pcb, enkoder.sch]
2020-12-25 Remove unnecessary gerber files
    [enkoder-B_Cu.gbr, enkoder-B_Mask.gbr, enkoder-B_SilkS.gbr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]
2020-12-25 Remove datasheets and pdfs from encoder folder
2020-12-26 Add Encoder message, fix .gitignore to include ros package.xml files, cleanup package.xml and CMakeLists.txt
    [statek.urdf]
2020-12-26 Add encoder publishers, fix URDF links and joints, add code to dynamic transform publisher
    [statek.urdf]
2020-12-30 Working on vision_publisher_node
    [statek.urdf]
2020-12-30 Add visual_publisher_node and calibration file
2021-01-10 Add multiple cameras to Gazebo
    [statek.urdf]
2021-01-10 Change CAD, add gerber zip files for electronics
    [converter_case.ipt, din_lamp_connector.ipt, enkoder.kicad_pcb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]
2021-01-13 Update instructions, add imu cad, add gearing cad
    [converter_case.ipt, converter_case.stl, imu_cable_holder.ipt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]
2021-01-13 Add encoder cover
    [converter_case.ipt, converter_case.stl, encoder_cover.ipt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]
2021-03-01 Add button panel, edit CAD models
    [button_panel.kicad_pcb, button_panel.sch, chassis.ipt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]
2021-03-07 Add battery basket and motor gearing CAD models
    [battery.ipt, battery_box.ipt, battery_box.stl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]
2021-03-07 Add connections schematic
    [12V battery left.sch, 12V battery right.sch, 16V Step down 300W.sch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]
2021-03-07 Add rosserial
    [statek.urdf]
2021-03-09 Add battery config
    [statek.urdf]
2021-03-09 Modify camera calibration launch file
2021-03-09 Add depth calibrator
2021-03-09 Work on camera calibrator
2021-03-09 Fix stereo_image_proc, change lidar's tf
2021-03-10 Fix urdf a bit, update real time code
    [main.cpp, motor_controller.cpp, motor_controller.hpp]
2021-03-10 Change motor control plugin
    [statek.urdf]
2021-03-10 Change rviz, change encoder transform publisher
2021-03-10 Working on wheel stabilizer
    [wheel_stabilizer.ipt, wheel_stabilizer.stl]
2021-03-10 Add velocity tester to RT code
2021-03-16 Edit button panel, edit CAD, add motor tensioners
    [Lidar.sch, button_panel.kicad_pcb, button_panel.sch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]
2021-03-27 Add motion calibrator
2021-03-27 Work on real time core
    [statek.urdf]
2021-03-27 Add chain guide models
    [12V battery left.sch, 12V battery right.sch, 16V Step down 300W.sch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]
2021-03-31 Add fake inertia
    [statek.urdf]
2021-03-31 Add name to config
    [robot_description.urdf]
2021-03-31 Add tf to statek_config, change Encoder msg
    [robot_description.urdf]
2021-04-01 Replace integral control with pid control
    [am4096.hpp, config.hpp, main.cpp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]
2021-04-02 Abandon mbed / gcc4mbed as it does not work with rosserial at all D:, switch to platrofmio and arduino
    [am4096.hpp, config.hpp, main.cpp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]
2021-04-02 Change motion config from state space to pid
2021-04-03 Add imu stuff, change platformio upload script a bit
    [upload.cfg]
2021-04-08 Add odometry
2021-04-08 Change connections
    [Big screw shield.sch, connections.sch]
2021-04-08 Fix step response identification, change some messages
    [am4096.hpp, main.cpp]
2021-04-10 Add imu and odom to param sender node
2021-04-10 Add PID autotuning
2021-04-11 Add smoothing factor to motor params
2021-04-24 Fix odometry compensation in mapper, add tf from sensor to footprint from mapper, add differential_to_twist_feedback node
2021-04-24 Add lidar to img node
2021-04-26 Fix motor control plugin
    [robot_description.urdf]
2021-04-26 Fix odometry
2021-04-26 Fix imu linear acceleration reading.
    [main.cpp]
2021-04-26 Add lidar dataset collector
2021-04-29 Change IMU param message
2021-04-29 Change imu params message
2021-04-29 Change map size, placed BOLD line drawing stuff before obstacle detection in raytrace in statek's local mapper, amplified PID values a bit in optimizer.
2021-04-29 Change set imu params
2021-04-29 Fix problem with IMU set_param service
    [motion_config.yaml]
2021-04-29 Fix problem with IMU set_params service
    [main.cpp]
2021-05-19 Add Kalman filter to gps_to_tf_node
2021-05-19 Change IMU update rate
2021-05-19 Update IMU ASAP, Change real time messages to float32 instead of float64
2021-07-14 Add MPC code, set infinity as no goal value in voronoi map, comment Kalman filter in GPS to tf node for now, fix some launch files, split statek_hw into some clearly distinguished launch files, chang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
    [robot_description.urdf]
2021-07-14 Add park map, force rviz markers to be visible until next update, work a bit with Gazebo urdf model
    [collision.blend, model.sdf, park.blend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]
2021-07-17 Fix nantransform in gps to tf node, change yaml configs a bit, tune mpc weights, add dynamic prediction horizon algorithm, move getTransform to separate thread in mpc and mappers for performance gains
    [motion_config.yaml]
2021-07-18 Update update mechanism in MPC, add mechanism to prevent stuck in some cases, change frame from map link to earth in short term planner node, change yaml configs
    [mpc_config.yaml]
2021-07-27 Change IMU in real time source
2021-08-09 Change imu angle reading in rt core
    [jetson_case_cover.ipt, motor_chain_guide_center.ipt, motor_chain_guide_center.stl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]
2021-08-13 General changes and bug fixing
    [motion_config.yaml]
2021-08-13 Add leg detector, change urdf a bit
2021-08-13 Working on leg detector
2021-08-17 Add queue_size for rospy subscribers where it was missing, work on leg_detector node, add lidar_img_config.yaml
    [encoders_wheels_transforms_publisher.py, lidar_img_config.yaml]
2021-08-18 Add bresenham filling to lidar_to_img node, add kalman filtering to leg_detector
2021-08-18 Edit laser_to_img config
2021-08-19 Work on leg detector
2021-09-02 Change yaml configs, change process and measurement variance to matrices in fix_to_tf, working on leg detector, remove ROS_WARN from MPC node
    [mpc_config.yaml]
2021-09-02 Retrained lidar network
2021-09-13 Move bresenham to abstract map, fuse static and dynamic maps, tune gps kalman, fix long term navigator
    [lidar_img_config.yaml]
2021-09-13 Change sim and urdf
